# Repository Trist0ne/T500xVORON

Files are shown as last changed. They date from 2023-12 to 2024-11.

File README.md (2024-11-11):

# T500xVORON

A Comgrow T500 Rework to install an RC8 Voron Stealthburner, complete with ChaoticLabs CNC Tap for nozzle based probing and Auto-Z offset, and CANBUS single cable intergration. This should be considered a moderately advanced build; you will need experience or be willing to learn configuring Klipper, crimping/soldering wire, using heat-set inserts, and be comfortable dissasembling/reassembling the T500. If your printer blows up into a million pieces (or otherwise doesn't work like you want it to), you are responsible. I've been running this setup for the better part of a year without issue, and there are several other VoronT500's out there in the wild running nicely. I did my best to document my process and make the configurations foolproof, but I may have missed something somewhere. You may need to use your brain a bit to troubleshoot! Respective rights and thanks go to the VORON team of course, as well as BTT and CHAOTICLABS for their documentation.

The guide below will cover the full T500 conversion; you may be able to deviate if you just want parts of it (for example; enabling sensorless homing on your stock T500) or you want to use different components (such as a different toolhead board, different CANBUS adapter, or not using CANBUS at all), but you're on your own if you do so.

## Why would I want this?
* VORON TAP is far more accurate than the stock inductive Z probe, and is not prone to thermal drift. 
* TAP allows for automatic Z offset, every print, regardless of print surface. "Always perfect first layers"!
* The modular design allows you to change out hotends easily, or use different hotend styles than the stock one. This also makes maintenance or failure recovery WAY easier.
* The LED's on the hotend can show the current printer status, change as the printer heats up to visually show temperature, and illuminate the nozzle while printing. 
* The VORON Stealthburner allows you to use more off-the-shelf, higher quality components that are easy to obtain and replace. It's difficult to get replacements for Comgrow proprietary parts (parts can take weeks to ship).
* An additional ADXL sensor on the X axis simplifies input shaping.
* Simplified wiring with CANBUS cuts the amount of wires running to the toolhead down to just one unified cable.
* It just damn **looks** cooler.

## TABLE OF CONTENTS
### [THINGS TO BUY](https://github.com/Trist0ne/T500xVORON/blob/main/README.md#things-to-buy)
### [THINGS TO PRINT](https://github.com/Trist0ne/T500xVORON/blob/main/README.md#things-to-print)
### [THE BUILD](https://github.com/Trist0ne/T500xVORON/blob/main/README.md#the-build)
#### [> PREREQUISITES](https://github.com/Trist0ne/T500xVORON/blob/main/README.md#prerequisites)
#### [> MOUNTING THE TOOLHEAD](https://github.com/Trist0ne/T500xVORON/blob/main/README.md#mounting-the-toolhead)
#### [> RAISING THE BED](https://github.com/Trist0ne/T500xVORON/blob/main/README.md#raising-the-bed)
#### [> WIRING WIRING WIRING](https://github.com/Trist0ne/T500xVORON/blob/main/README.md#wiring-wiring-wiring)
#### [> SOFTWARE CONFIGURATION](https://github.com/Trist0ne/T500xVORON/blob/main/README.md#software-configuration)
#### [> SLICER CONFIGURATION](https://github.com/Trist0ne/T500xVORON/blob/main/README.md#slicer-configuration)
#### [> TROUBLESHOOTING NOTES](https://github.com/Trist0ne/T500xVORON/blob/main/README.md#troubleshooting-notes)

## Things to Buy
* [ChaoticLabs CNC TAP **V2**](https://chaoticlab.xyz/products/cnc-voron-tap). This is the nozzle probing system. It MUST be the V2
* [BTT U2C V2.1 CANBUS USB adapter](https://www.amazon.com/BIGTREETECH-Adapter-Supports-Connection-Interface/dp/B0B1X47319). This is the USB to CANBUS adapter
* [BTT SB 2209 RP2040](https://biqu.equipment/products/bigtreetech-ebb-sb2209-can-v1-0?variant=40377392431202). This is the toolhead control board. You should get the 2209 **RP2040** variant.
* [Everything from Fasteners & Electronics section of the BOM of the latest VORON Stealthburner](https://vorondesign.com/voron_stealthburner). Do not cheap out on the BMG extruder kit!
* [A Stealthburner compatible Hotend of your choosing](https://us.store.bambulab.com/products/complete-hotend-assembly-x1-series). I use the Bambu Labs hardened steel hotend assembly, but any stealthburner compatible hotend will work.
  * If you use a Bambu Labs hotend, [this](https://www.printables.com/model/322091-voron-stealthburner-printhead-for-bambu-x1cx1-hote) adapter for the StealthBurner works well!
* A few extra parts you will need:
  * 4x M3 5x4mm heat set inserts (same ones that VORONs use)
  * 8x M4x40mmm Socket Heat Cap Screws (Or whatever style M4x40mm screws you would like, SHCS's are just the easiest to tighten during the build)
  * A small length of PTFE tubing for the Stealthburner hotend mount
  * A small spool of 20 AWG wire
  * A small length of double sided mounting tape

## Things to Print
**THESE MUST ALL BE PRINTED FROM ABS OR ASA. THEY ARE DESIGNED FOR ABS. OTHER MATERIALS ARE NOT SUITABLE EITHER DUE TO THEIR TEMPERATURE RESISTANCE OR STRUCTURE CREEP OVER TIME; YOU HAVE BEEN WARNED**
* [1x Complete Voron Stealthburner Assembly](https://github.com/VoronDesign/Voron-Stealthburner/tree/main)
  * Optionally [but highly reccomended!] use the inline filament runout sensor located [here](https://www.printables.com/model/292186-stealthburner-clockwork-2-filament-sensor/files). This replaces the main_body of the CW2 extruder.
  * Ensure you use the Cable_Cover_for_PCB and the toolhead PCB spacer!
  * You do not need to print the gantry mount or TAP mount; the extruder and toolhead cover screw directly into the CNC TAP
* [1x Toolhead Adapter Plate](https://github.com/Trist0ne/T500xVORON/blob/main/STL/Toolhead%20Adapter%20Plate.stl)
* [2x Bed Spacers](https://github.com/Trist0ne/T500xVORON/blob/main/STL/Bed%20Spacer%20T500%20v3.stl). Ensure these print perfectly flat with no warping, or it will throw off your bed level!
* [1x CW2 Cable Bridge](https://github.com/bigtreetech/EBB/blob/master/EBB%20SB2240_2209%20CAN/STL/CW2%20Cable%20Bridge.STL)
* [1x CAN Cable Strain Relief](https://github.com/bigtreetech/EBB/blob/master/EBB%20SB2240_2209%20CAN/STL/Printed_Part_for_CAN_Cable_V1.2.stl)
* [1x U2C Adapter Plate](https://www.printables.com/model/422274-bigtreetech-u2c-mount/files)
  * You will also need some double sided mounting tape to secure this in the electronics bay

Print Settings:
* Layer height: 0.2mm
* Extrusion width: 0.4mm, forced
* Infill percentage: 40%
* Infill type: grid, gyroid, honeycomb, triangle, or cubic
* Wall count: 4
* Solid top/bottom layers: 5
* Supports: NONE

## The Build
You can do the following sections in any order, they are just listed in the order I did them. **Some of the steps will be linked to other guides** for the non-T500 conversion specific parts as they cover them more in depth, and there's no need to reinvent the wheel.

### Prerequisites
* Flash both KATAPULT and Klipper to the U2C CANBUS adapter AND the SB2209 Toolhead board
  * To make your life easier, do this before assembling anything.
  * An excellent resource for CANBUS flashing I reccomend following is located [here](https://github.com/Esoterical/voron_canbus). There are subfolders for the [U2C](https://github.com/Esoterical/voron_canbus/tree/main/can_adapter/BigTreeTech%20U2C%20v2.1) and the [SB2209 rp2040](https://github.com/Esoterical/voron_canbus/tree/main/toolhead_flashing/common_hardware/BigTreeTech%20SB2209%20(RP2040)).
  * You may get stuck here for a bit; this can be a little tricky if you've never done it before, but its not overly difficult. Follow the guide linked above carefully, as the documentation that comes with the boards is a little out of date. Technically you can skip installing KATAPULT and just flash Klipper directly, but it will make updating klipper significantly more difficult later.
  * Technically, flashing Klipper to the U2C is optional. You can probably comment out the "u2c.cfg" and go about your life; it just lets you update and manage it easier, and see it as a temperature sensor in Mainsail. [This](https://docs.meteyou.wtf/btt-u2c-v2.x/klipper-usb-to-can/) guide can help if you get stuck flashing Klipper to the U2C.
  * Pro tip- flashing on the SB2209 rp2040 takes a SECOND. I reran the process many times becuase I thought surely it was failing, but it really does just take a moment to flash. 
* Assemble the VORON Stealthburner
  * Follow the build guide located [here](https://github.com/VoronDesign/Voron-Stealthburner/tree/main/Manual). This is a large step, and your toolhead will only function as well as you assemble it, so take your time.
  * Attach and wire the SB2209 to the Stealthburner, following the build guide [here](https://github.com/bigtreetech/EBB/blob/master/EBB%20SB2209%20CAN%20(RP2040)/Build%20Guide/EBB%20SB2209%20CAN%20V1.0（RP2040）BUILD%20GUIDE_1129.pdf); double check your wiring carefully for the CNC-TAP especially. The colors may not be standard on your TAP wiring, and putting them in the wrong order can fry your TAP sensor.

### Mounting the Toolhead
1. Start by inserting {4x} M3 5x4mm heat set inserts into the adapter plate. Take care to ensure they are perfectly level with the surface of the plastic.

(Ignore the very bottom two holes in the picture; they didn't make it into the final design)

3. Unclip the stock toolhead umbilical and drag chain mount, and move them out of the way. Unmount the stock T500 toolhead and drag chain plate. There are 4 screws around the outside of the plastic casing (keep these!), several screws holding the drag chain plate to the rail. You should be left with a metal rectangular sliding rail.


4. Using the 4 casing screws from the stock toolhead, attach the Adapter Plate to the rectangular sliding rail. Check to ensure the rail still slides back and forth. 


5. Attach the ChaoticLabs CNC TAP to the Adapter Plate
   * The attachment process is the same as the one located in the [CNC TAP build guide](https://github.com/Chaoticlab/CNC-Tap-for-Voron/blob/master/Manual/CNC_Voron_Tap_V2_Build_Guide_20231013.pdf)

6. Attach the Stealthburner assembly to the CNC TAP. Check to make sure the whole assembly can slide up and down (the 'TAP' function)
   * The attachment process for the Stealthburner is the same as the one located in the [CNC TAP build guide](https://github.com/Chaoticlab/CNC-Tap-for-Voron/blob/master/Manual/CNC_Voron_Tap_V2_Build_Guide_20231013.pdf)
   * Ensure you attach the cable bridge shown at the end of the build guide. We will not use the steel wire, but the bridge will provide strain relief and stability to the CANBUS cable port.


7. Check clearences, and appreciate how nice the Stealthburner looks mounted on the T500

### Raising the Bed
The stock T500 gantry and bed are mounted in such a way that the gantry cannot drop low enough to touch the nozzle to the bed. Obviously, this is problematic. Because of the way the gantry is designed, there is no easy way to gracefully drop the toolhead low enough; thus, we have to go the other direction and raise the bed!
* "Wont I lose Z height??"
  * Nope! In it's stock form, the T500 Z rails can raise the nozzle up to 550mm. With these spacers in place, you will still have 520mm of Z clearance (though it will still be software limited to 500mm), so there is no lost Z build height!
* "Wont these spacers melt so close to the bed? Are they strong enough?"
  * Nope! They're far enough from the bed that they are well within the longterm operating temperature limit of ABS. ABS also does not stress creep over time, and should remain durable for the life of the printer
 
1. Remove the print surface, and remove the 8x M4 socket head screws using the access holes
   * 

   * If you have a difficult time getting a tool to fit in those holes, you can unbolt every M4 countersunk screw and remove the headbed entirely.
   * If you remove the bed from the bed frame, remove the screws holding the bed drag chain to the bed frame
   * 

2. Carefully raise the bed frame, and align the bed spacers to the long rectangular rails
   * Be very careful not to damage the heatbed wiring!


   * Depending on how much your ABS print shrunk, you may need to slightly drill out the holes in the printed bed spacers; you'll never get them properly aligned unless the screws can slide through the spacers with only light resistance


3. Using 8x M4x40mm screws, bolt the bed frame to the Y axis rails through the spacers. Ensure everything is very tight and does not have any play; you dont want your bed level changing or your bed flying off its rails!


4. If you removed it in step 1, reattach the drag chain to the bed frame

5. Check to ensure the bed is able to slide **all** the way back and forth across its rails. If you did not use M4x40mm screws to attach the spacers, they may stick out from the rails and hit the Y Stepper drivers.

### Wiring Wiring Wiring
Thankfully for the most part we are SIMPLIFYING the wiring rather than making it more complicated. It should go without saying that your printer should be **fully powered off and unplugged** for the next few steps especially.

#### U2C Wiring and Mounting
1. Remove the electronics bay cover
  * There are 6 screws, 4 in the front and two in the back
  * You will have to slide the heatbed back and forth to reach them all

2. Carefully unplug and remove the following items from the printer. You will need to cut zip ties and undo screws where appropriate:
* The stock toolhead umbilical (you will need to cut open the Z axis wiring loom to remove this fully. Do NOT cut or remove the X axis stepper wires)
  * Remove the umbilical from the X axis drag chain; we will still utilize the drag chain. Unscrew the mounts on the drag chain and move it as close to the Z axis rails as you can, then reattach it 
* The X and Y axis endstops (you will need to cut open the Z axis wiring loom to remove this fully. Do NOT cut or remove the X axis stepper wires)
* 

* Flick the switch highlighted below to "ON" to enable sensorless homing
* 

3. Using at least 20 AWG wire, connect the U2C to the T500 power supply
* There are two open attachment points for power and ground on the stock power supply you can utilize. This is an example; please pay attention to which one is negative and which one is positive
* 

* Connect the wires from the +/- power supply to the green VIN/GND points on the U2C
* 
* Do not get them backwards unless you want to fry your boards!!!

4. Insert the jumper included with the U2C on the pins labled 120R, near the USB-C port

5. Mount the U2C in the electronics bay using the printed mount and double sided tape to secure it
* I chose to mount it here 21556689-9E68-4C35-BBAF-199B8BBE90C0_1_201_a

6. Run a USB-C to USB-A cable from the U2C an open USB port under the T500 screen, following the existing cable routing path from the stock mainboard. Zip tie up the excess; keep it neat!

#### Toolhead CANBUS Cable

1. Crimp the end of the long cable included with the SB2209 with the Molex Microfit 4 pin connector that came with the U2C. Take great care that you align CAN_L, CAN_H, GND, and VIN appropriatly (see pinout above; the black 4 pin connector next to the large white one), or you will pop your toolhead board.
* You do not need to shorten the cable; there is room in the electronics back to tuck the slack away nicely.

2. Using the screws on top of the Z axis, move the toolhead mount as far up the Z axis and as far to the right of the X axis as it will go.
* This will determine how much cable length you need

3. Thread the CANBUS cable from the toolhead port through the X axis drag chain, following the same path the stock umbilical cable did into the electronics bay. Use the same anchor points to attach the cable to the edge of the X axis and the bottom of the Z axis
* LEAVE SOME ROOM FOR SLACK. While you want these cables managed nicely, you dont want them routed so tightly that they're damaging the things they're attached to, or the internal wiring. Dont attach it so tightly that the Z axis rips the cable out at max height!
* Route the cable cleanly through the electronics bay to the U2C. Plug it in, then zip tie up the rest of the slack to one of the stock anchor points.
* Zip tie the CANBUS cable to the X axis stepper wire to keep everything clean and organized
* Finally, Zip tie the CANBUS cable to the edge of the drag chain. The plasic mount on the EBB cable will provide plenty of strain relief 0A58DF86-1371-48C0-9A15-90A06EAC607F_1_201_a

#### Wiring Checks
Dont think, just double check them
1. Power supply POSITIVE is wired to U2C VIN. Power supply GROUND is wired to U2C GND
2. CAN_L, CAN_H, GND, and VIN on the CANBUS cable are aligned to the CAN_L, CAN_H, GND, and VIN pins on the U2C

When you're 100% sure everything is lined up, plug your printer in and flip the power on. Check to make sure the stock mainboard, the U2C and the SB2209 all light up (and that nothing goes pop!). When you're satisfied with your work, reinstall the electronics bay cover and screw it back down. 

### Software Configuration

#### Initial Startup
1. SSH into your printer. The username is **mks**, and the password is **makerbase**. Install KAMP on your printer, located [here](https://github.com/kyleisah/Klipper-Adaptive-Meshing-Purging)
2. Access your printers web-ui. In the machine tab, delete ALL the config files.
3. Download the Klipper Configurations folder from this Github ([here](https://github.com/Trist0ne/T500xVORON/tree/main/Klipper%20Configurations)), and upload them ALL to the printer's config section.
* 
3. Configure the annotated sections of **printer.cfg**, **toolboard.cfg**, and **u2c.cfg**. You will need to fill in the canbus_uuid sections to to tell your printer the CAN addresses of your U2C and SB2209, as well as configuring your sensorless homing (info below)
4. Save and click 'firmware restart'; resolve any errors that Klipper may throw, if any (the error message will tell you what the configuration issue is).

#### Z Endstop Check
**DO THIS BEFORE ATTEMPTING TO HOME THE PRINTER**
1. Once Klipper has successfully loaded and can interface with the U2C and SB2209, navigate to the machine page of the web UI and press 'sync endstops'
2. Endstop Z should be 'OPEN'
3. By hand, move the toolhead up to the top of it's travel to trigger the CNC TAP sensor. Hold it in place and click the 'sync enstops' button. Endstop Z should now be marked as 'CLOSED'
4. Additionally, there should be a blue light on the rear of the TAP sensor that turns red when triggered. If this doesn't happen, you've either wired the sensor wrong or it is faulty.

#### Sensorless Homing Configuration
**DO THIS BEFORE ATTEMPTING TO HOME THE PRINTER**
1. Follow the guide located [here](https://docs.vorondesign.com/community/howto/clee/sensorless_xy_homing.html) to calibrate the sensorless homing.
* The default configurations are made to work with sensorless homing, and are largely preconfigured. You can start from "Finding the right StallGuard threshold". You do not need to add sensorless homing macros, I built them in. Ensure that your sensitivity numbers are high enough that you do not damage the printer, but low enough that the machine is consistently able to home itself.

#### Z Offset Configuration
Update your Z offset
* Remember, with Tap, your nozzle IS the probe. You'll need to manually calibrate the probe's Z offset by using PROBE_CALIBRATE and your chosen leveling method (I use a sheet of paper)

### Final Checks
1. Ensure that your printer can reliably home X, Y, and Z.
2. Test that your Extruder, Hotend, Hotend Fan, Part Cooling Fan, and [optionally] the runout sensor all work as expected.
3. PID Calibrate your Hotend following [this guide](https://www.obico.io/blog/klipper-pid-tuning/)
4. Follow the [Ellis3dp print tuning guide](https://ellis3dp.com/Print-Tuning-Guide/articles/extruder_calibration.html) to dial in your Stealthburner
5. Configure Input Shaping on both X and Y
* You can reference [this guide](https://www.klipper3d.org/Measuring_Resonances.html#bed-slinger-printers) for help
* Your X axis now has a built in accelerometer. You will still need to plug in the included accelerometer and mount it on the Y axis, the same way you would do on the stock T500.
* I use the SHAPER_CALIBRATE macro for automatic calibration. It will measure both X and Y sequentially and apply the best settings automatically. 

6. Retune your Pressure Advance
* Follow [this guide](https://github.com/SoftFever/OrcaSlicer/wiki/Calibration) from the Orca Slicer wiki. You shold set this number in the Orca Slicer filament profile settings, rather than setting it in the Klipper configs. It will be different for every filament and between brands. 
7. Pat yourself on the back for a job well done! Edit your slicer settings as shown below, and then do a test print!

### Slicer Configuration
1. Edit your printer settings "Machine G-code" tab as follows:
* PRINT_START EXTRUDER=[nozzle_temperature_initial_layer] BED=[bed_temperature_initial_layer_single] CHAMBER=[chamber_temperature]
* PRINT_END
* 
2. In the 'Quality' tab, enable Arc Fitting
3. In the 'Others' tab, enable
* Label Objects
* Exclude Objects

### Troubleshooting Notes
There are two errors you may see in your console when starting a print:
1. Unknown command:"SAVE_LAST_FILE"
2. Error evaluating 'gcode_macro PRINT_START:gcode': jinja2.exceptions.UndefinedError: 'dict object' has no attribute 'BED'
These are caused by the non-standard version of klipperscreen that comes built into the T500, and makes calls to incorrectly labeled markers. **Thankfully, they don't actually impede the printing, so you can ignore them!** You can resolve this by installing the standard version of KlipperScreen using [KIAUH](https://github.com/dw-0/kiauh), which comes built into the T500

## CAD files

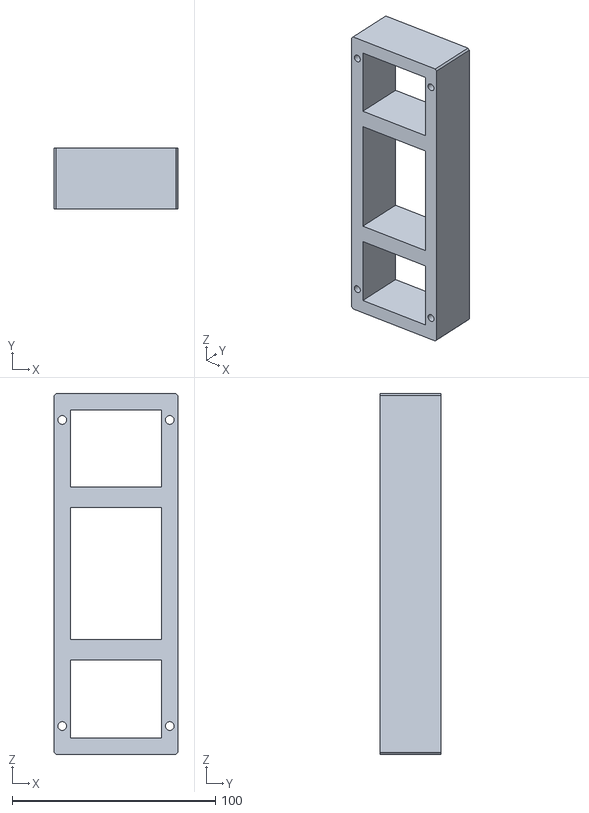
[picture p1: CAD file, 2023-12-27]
STL/Bed Spacer T500 v3.stl
60.9 x 30.0 x 177.5

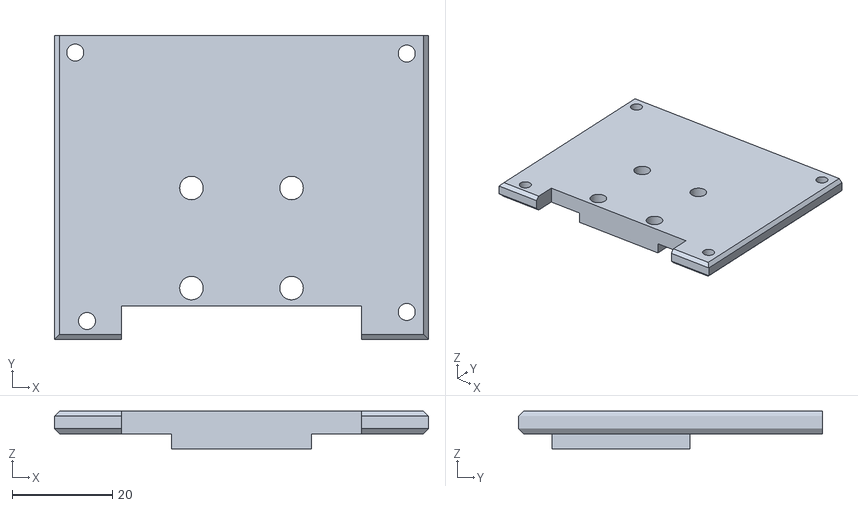
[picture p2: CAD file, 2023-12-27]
STL/Toolhead Adapter Plate.stl
74.8 x 60.7 x 7.50

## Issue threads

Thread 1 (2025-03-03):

Settings for PT1000 Temperature probe

gsargent70, 2025-03-03:
If you are going to use a PT1000 or PT100 temperature probe on your hot end you will need to make the following changes for this guide.

On the SB2209 rp2040 board you will need to wire your probe to the four pin connector rather than the two pin connector.  Please follow the documentation in the SB2209 build guide to see the proper way to crimp your cable.

In the ToolBoard.cfg file you will need to do the following:

In the extruder section comment out sensor_type and sensor_pin lines

Add the following lines to the extruder section

sensor_type: MAX31865
sensor_pin: ToolBoard:gpio9
spi_software_sclk_pin: ToolBoard:gpio10
spi_software_mosi_pin: ToolBoard:gpio8
spi_software_miso_pin: ToolBoard:gpio11
rtd_nominal_r: 100
rtd_reference_r: 430
rtd_num_of_wires: 2

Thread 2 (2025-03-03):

Python 3.8 needed error after updating Klipperscreen

gsargent70, 2025-03-03:
If you decide to update Klipperscreen to eliminate the errors listed in this guide from it being on an old version, you will receive an error about the new version of Klipperscreen needing Python 3.8

Unfortunately there is no good way to update to Python 3.8 with the version of debian on the T500 pad.

To solve this perform these steps after updating Klipperscreen

Log in to the T500 pad via SSH

Enter the following two lines

cd ~/KlipperScreen
git reset --hard v0.4.1

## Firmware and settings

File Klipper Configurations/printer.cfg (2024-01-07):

## CREATED BY @Trist0ne

########################################################################################################################### CONFIG INCLUDES

[include KAMP_Settings.cfg]
[include start.cfg]
[include runout.cfg] ## If you do not use a runout sensor, comment this one out
[include macros.cfg]
[include u2c.cfg]
[include toolboard.cfg]
[include stealthburner_leds.cfg]
[include temperature_led.cfg]

########################################################################################################################### MCU

[mcu]
serial:/dev/serial/by-id/usb-1a86_USB_Serial-if00-port0
restart_method: command

[mcu rpi]
serial: /tmp/klipper_host_mcu

########################################################################################################################### SPEED/ACCEL SETTINGS

[printer]
kinematics: cartesian
max_velocity: 300
max_accel: 3000
max_accel_to_decel: 1500
max_z_velocity: 15
max_z_accel: 100
#square_corner_velocity:2

########################################################################################################################### POWER-ON GCODE

[delayed_gcode set_temeperature_leds]
initial_duration: 1
gcode:
     STATUS_READY

########################################################################################################################### MAINSAIL MISC

[virtual_sdcard]
path: ~/printer_data/gcodes
on_error_gcode: CANCEL_PRINT

[exclude_object]

[pause_resume]

[display_status]

[gcode_arcs]
resolution: 0.1

[idle_timeout]
timeout: 3600 # Idle time (in seconds). This is just the default; it is extended out to 12 hours by the PAUSE macro

########################################################################################################################### INPUT SHAPER

[adxl345 bed]
cs_pin: rpi:None
spi_bus: spidev0.0

[adxl345 hotend]
cs_pin: ToolBoard:gpio1
spi_software_sclk_pin: ToolBoard:gpio2
spi_software_mosi_pin: ToolBoard:gpio0
spi_software_miso_pin: ToolBoard:gpio3

[input_shaper] # Auto configured at the bottom of the config. CONFIGURE YOUR OWN INPUT SHAPER
#shaper_type_x = 3hump_ei
#shaper_freq_x = 52.4
#shaper_type_y = 2hump_ei
#shaper_freq_y = 25

[resonance_tester]
accel_chip_x: adxl345 hotend
accel_chip_y: adxl345 bed
probe_points:250, 250, 20  # an example
accel_per_hz:50
min_freq:1
max_freq:100
max_smoothing:0.2
hz_per_sec:0.5

########################################################################################################################### HEATER CHECKS

[verify_heater extruder]
max_error: 60
check_gain_time:20
hysteresis: 5
heating_gain: 2

[verify_heater heater_bed]
max_error: 240
check_gain_time:180
hysteresis: 5
heating_gain: 1 

########################################################################################################################### STEPPER X

[stepper_x]
step_pin: PE2
dir_pin: PE0
enable_pin: !PE3
microsteps: 16
rotation_distance: 72
endstop_pin: tmc2209_stepper_x:virtual_endstop
#endstop_pin: ^PE15
position_endstop: -6
position_min: -6
position_max: 505
homing_speed: 80
homing_retract_dist: 2
step_pulse_duration:0.000002

[tmc2209 stepper_x]
uart_pin: PE1
diag_pin: ^PE15 # use the same pin that was previously the endstop_pin!
driver_SGTHRS: 255 # 255 is most sensitive value, 0 is least sensitive. Calibrate this yourself
run_current: 1.5
uart_address: 3
#stealthchop_threshold: 999999
driver_TBL: 2
driver_TOFF: 2
driver_HEND: 1
driver_HSTRT: 4
driver_PWM_LIM: 8 
driver_PWM_GRAD: 8
driver_PWM_FREQ: 1
driver_PWM_REG: 4

########################################################################################################################### STEPPER Y

[stepper_y]
step_pin: PB8
dir_pin: !PB6
enable_pin: !PB9
microsteps: 16
rotation_distance: 72
#endstop_pin: ^PE13
endstop_pin: tmc2209_stepper_y:virtual_endstop 
position_endstop: -10
position_min: -10
position_max: 500
homing_speed: 50
homing_retract_dist: 0
step_pulse_duration:0.000002

[tmc2209 stepper_y]
uart_pin: PB7
diag_pin: ^PE13 # use the same pin that was previously the endstop_pin!
driver_SGTHRS: 255 # 255 is most sensitive value, 0 is least sensitive. Calibrate this yourself!
run_current: 1.5
uart_address: 3
#stealthchop_threshold: 999999

[stepper_y1]
step_pin:PD7
dir_pin:PD0
enable_pin:!PB5
microsteps:16
rotation_distance:72
#endstop_pin: ^PE13
endstop_pin: tmc2209_stepper_y:virtual_endstop

[tmc2209 stepper_y1]
uart_pin:PD1
#diag_pin: ^PE13 # use the same pin that was previously the endstop_pin!
#driver_SGTHRS: 255 # 255 is most sensitive value, 0 is least sensitive
run_current:1.5 
uart_address:3
#stealthchop_threshold: 999999

########################################################################################################################### STEPPER Z

[stepper_z]
step_pin: PD15
dir_pin: !PD13
enable_pin: !PA12
microsteps: 16
rotation_distance: 4
endstop_pin:probe:z_virtual_endstop
position_max: 505
position_min: -3
homing_speed: 20

[tmc2209 stepper_z]
uart_pin:PD14
run_current:0.6
uart_address:3
stealthchop_threshold: 999999

[stepper_z1]
step_pin: PD11
dir_pin: !PD9
enable_pin: !PD12
microsteps: 16
rotation_distance: 4
endstop_pin:probe:z_virtual_endstop

[tmc2209 stepper_z1]
uart_pin:PD10
run_current:0.6
uart_address:3
stealthchop_threshold: 999999

########################################################################################################################### BED HEATER

[heater_bed]
heater_pin: PA0
sensor_type: EPCOS 100K B57560G104F
sensor_pin: PC5
#control: pid
#pid_Kp: 75.227
#pid_Ki: 0.807
#pid_Kd: 1748.382
min_temp: 0
max_temp: 95
pwm_cycle_time: 0.0166

########################################################################################################################### Z HOMING

[safe_z_home]
home_xy_position: 250,250
speed: 90
z_hop: 5                 # Move up 5mm
z_hop_speed: 5

########################################################################################################################### PROBE

[probe]
pin: !ToolBoard:gpio22
x_offset: 0
y_offset: 0
z_offset: 0.5 ## CONFIGURE THIS WITH THE Z CALIBRATE TOOL
speed: 10.0
samples: 3
samples_result: median
sample_retract_dist: 3.0
samples_tolerance: 0.006
samples_tolerance_retries: 10
activate_gcode:
    {% set PROBE_TEMP = 180 %}
    {% set MAX_TEMP = PROBE_TEMP + 5 %}
    {% set ACTUAL_TEMP = printer.extruder.temperature %}
    {% set TARGET_TEMP = printer.extruder.target %}

    {% if TARGET_TEMP > PROBE_TEMP %}
        { action_respond_info('Extruder temperature target of %.1fC is too high, lowering to %.1fC' % (TARGET_TEMP, PROBE_TEMP)) }
        M109 S{ PROBE_TEMP }
    {% else %}
        # Temperature target is already low enough, but nozzle may still be too hot.
        {% if ACTUAL_TEMP > MAX_TEMP %}
            { action_respond_info('Extruder temperature %.1fC is still too high, waiting until below %.1fC' % (ACTUAL_TEMP, MAX_TEMP)) }
            TEMPERATURE_WAIT SENSOR=extruder MAXIMUM={ MAX_TEMP }
        {% endif %}
    {% endif %}

########################################################################################################################### BED MESH

[bed_mesh]
speed:190                
horizontal_move_z:3   
mesh_min:26,26   
mesh_max:478,474 
probe_count:10,10    ## you can raise or lower the amount of points probed to speed up meshing or increase mesh accuracy
mesh_pps: 2, 3
algorithm: bicubic
bicubic_tension: 0.2 

########################################################################################################################### Z TILT

[z_tilt]
z_positions: 97, 250
             409, 250
points: 97, 250
        409, 250
speed: 200
horizontal_move_z: 5
retries: 20
retry_tolerance: .001

########################################################################################################################### MAINBOARD FANS

[controller_fan Fan_Board]
pin:PA3
fan_speed: 1.0
idle_timeout: 120
heater: heater_bed, extruder
stepper: stepper_x, stepper_y, stepper_y1, stepper_z, stepper_z1



########################################################################################################################### AUTO GENERATED

#*# <---------------------- SAVE_CONFIG ---------------------->
#*# DO NOT EDIT THIS BLOCK OR BELOW. The contents are auto-generated.
#*#
#*# [extruder]
#*#
#*# [bed_mesh default]
#*# version = 1
#*# points =
#*# 	0.174438, 0.175688, 0.181938
#*# 	0.170688, 0.176938, 0.184438
#*# 	0.193188, 0.194438, 0.198188
#*# x_count = 3
#*# y_count = 3
#*# mesh_x_pps = 4
#*# mesh_y_pps = 4
#*# algo = lagrange
#*# tension = 0.3
#*# min_x = 234.99
#*# max_x = 265.01
#*# min_y = 234.99
#*# max_y = 265.01
#*#
#*# [input_shaper]
#*# shaper_type_x = 2hump_ei
#*# shaper_freq_x = 61.4
#*# shaper_type_y = zv
#*# shaper_freq_y = 30.8
#*#
#*# [heater_bed]
#*# control = pid
#*# pid_kp = 74.862
#*# pid_ki = 0.558
#*# pid_kd = 2509.734

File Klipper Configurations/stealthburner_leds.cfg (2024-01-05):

# Macros for setting the status leds on the Voron StealthBurner toolhead (or for any neopixel-type leds).
#
# You will need to configure a neopixel (or other addressable led, such as dotstar). See
# https://www.klipper3d.org/Config_Reference.html#neopixel for configuration details.


#####################################
#           INSTRUCTIONS            #
#####################################
# How to use all this stuff:
#
#     1.  Copy this .cfg file into your Klipper config directory and then add [include stealthburner_leds.cfg]
#         to the top of your printer.cfg in order to register the LEDs and macros with Klipper.
#     2.  Define your LEDs by editing [neopixel sb_leds] below and entering the data pin from your control board
#         as well as the color order.
#
#           Note: RGB and RGBW are different and must be defined explicitly.  RGB and RGBW are also not able to 
#                 be mix-and-matched in the same chain. A separate data line would be needed for proper functioning.
#
#                 RGBW LEDs will have a visible yellow-ish phosphor section to the chip.  If your LEDs do not have
#                 this yellow portion, you have RGB LEDs.
#
#     3.  Save your config and restart Klipper.
#
#           Note: We set RED and BLUE to 1.0 to make it easier for users and supporters to detect 
#                 misconfigurations or miswiring. The default color format is for Neopixels with a dedicated 
#                 white LED. On startup, all three SB LEDs should light up.
#
#                 If you get random colors across your LEDs, change the color_order to GRB and restart. Then
#                 omit the W for each suggested color_order in the next paragraph.
#
#                 If you get MAGENTA, your  color order is correct. If you get CYAN, you need to use RGBW. If
#                 you get YELLOW, you need to use BRGW (note that BRG is only supported in the latest Klipper
#                 version).
#
#     4.  Once you have confirmed that the LEDs are set up correctly, you must now decide where you want 
#         these macros called up...which means adding them to your existing gcode macros.  NOTHING will happen
#         unless you add the STATUS_????? macros to your existing gcode macros.  
#
#           Example: add STATUS_LEVELING to the beginning of your QGL gcode macro, and then add STATUS_READY 
#                    to the end of it to set the logo LED and nozzle LEDs back to the `ready` state.
#
#           Example: add STATUS_CLEANING to the beginning of your nozzle-cleaning macro, and then STATUS_READY
#                    to the end of it to return the LEDs back to `ready` state.
#
#     5.  Feel free to change colors of each macro, create new ones if you have a need to.  The macros provided below
#         are just an example of what is possible.  If you want to try some more complex animations, you will most
#         likely have to use WLED with Moonraker and a small micro-controller 
#
#####################################
#       END INSTRUCTRUCTIONS        #
#####################################


[neopixel sb_leds]
pin: ToolBoard:gpio16
#   The pin connected to the neopixel. This parameter must be provided.
chain_count: 3
#   The number of Neopixel chips that are "daisy chained" to the
#   provided pin. The default is 1 (which indicates only a single
#   Neopixel is connected to the pin).
color_order: GRBW
#   Set the pixel order required by the LED hardware. Options are GRB,
#   RGB, GRBW, or RGBW. The default is GRB.
initial_RED: 0.0
initial_GREEN: 0.0
initial_BLUE: 0.0
initial_WHITE: 1.0
#   Sets the initial LED color of the Neopixel. Each value should be
#   between 0.0 and 1.0. The WHITE option is only available on RGBW
#   LEDs. The default for each color is 0.#

# Most configuration for the macros can be done by modifying the variables in the _sb_vars macro
# at the start of this file.

##########
# MACROS #
##########

# The following status macros are available (these go inside of your macros):
#
#    STATUS_READY
#    STATUS_OFF
#    STATUS_BUSY
#    STATUS_HEATING
#    STATUS_LEVELING
#    STATUS_HOMING
#    STATUS_CLEANING
#    STATUS_MESHING
#    STATUS_CALIBRATING_Z
#
# With additional macros for basic control:
#
#    SET_NOZZLE_LEDS_ON
#    SET_LOGO_LEDS_OFF
#    SET_NOZZLE_LEDS_OFF
#
# Contributed by Voron discord users wile.e, Tetsunosuke, and etherwalker


[gcode_macro _sb_vars]
# User settings for the StealthBurner status leds. You can change the status colors and led
# configurations for the logo and nozzle here.
variable_colors: {
        'logo': { # Colors for logo states
            'busy': {'r': 0.4, 'g': 0.0, 'b': 0.0, 'w': 0.0},
            'cleaning': {'r': 0.0, 'g': 0.02, 'b': 0.5, 'w': 0.0},
            'calibrating_z': {'r': 0.8, 'g': 0., 'b': 0.35, 'w': 0.0},
            'heating': {'r': 0.3, 'g': 0.18, 'b': 0.0, 'w': 0.0},
            'homing': {'r': 0.0, 'g': 0.6, 'b': 0.2, 'w': 0.0},
            'leveling': {'r': 0.5, 'g': 0.1, 'b': 0.4, 'w': 0.0},
            'meshing': {'r': 0.2, 'g': 1.0, 'b': 0.0, 'w': 0.0},
            'off': {'r': 0.0, 'g': 0.0, 'b': 0.0, 'w': 0.0},
            'printing': {'r': 1.0, 'g': 0.0, 'b': 0.0, 'w': 0.0},
            'standby': {'r': 0.00, 'g': 0.5, 'b': 0.5, 'w': 0.0},
        },
        'nozzle': { # Colors for nozzle states
            'heating': {'r': 0.8, 'g': 0.35, 'b': 0.0, 'w':0.0},
            'off': {'r': 0.0, 'g': 0.0, 'b': 0.0, 'w': 0.0},
            'on': {'r': 0.8, 'g': 0.8, 'b': 0.8, 'w':1.0},
            'standby': {'r': 0.0, 'g': 0.0, 'b': 0.0, 'w':0.0},
        },
        'thermal': {
            'hot': {'r': 1.0, 'g': 0.0, 'b': 0.0, 'w': 0.0},
            'cold': {'r': 0.3, 'g': 0.0, 'b': 0.3, 'w': 0.0}
        }
    }
variable_logo_led_name:         "sb_leds" 
# The name of the addressable LED chain that contains the logo LED(s)
variable_logo_idx:              "1" 
# A comma-separated list of indexes LEDs in the logo
variable_nozzle_led_name:       "sb_leds"
# The name of the addressable LED chain that contains the nozzle LED(s). This will
# typically be the same LED chain as the logo.
variable_nozzle_idx:            "2,3"
# A comma-separated list of indexes of LEDs in the nozzle
gcode:
    # This section is required.  Do Not Delete.


[gcode_macro _set_sb_leds]
gcode:
    {% set red = params.RED|default(0)|float %}
    {% set green = params.GREEN|default(0)|float %}
    {% set blue = params.BLUE|default(0)|float %}
    {% set white = params.WHITE|default(0)|float %}
    {% set led = params.LED|string %}
    {% set idx = (params.IDX|string).split(',') %}
    {% set transmit_last = params.TRANSMIT|default(1) %}

    {% for led_index in idx %}
        {% set transmit=transmit_last if loop.last else 0 %}
        set_led led={led} red={red} green={green} blue={blue} white={white} index={led_index} transmit={transmit}
    {% endfor %}

[gcode_macro _set_sb_leds_by_name]
gcode:
    {% set leds_name = params.LEDS %}
    {% set color_name = params.COLOR %}
    {% set color = printer["gcode_macro _sb_vars"].colors[leds_name][color_name] %}
    {% set led = printer["gcode_macro _sb_vars"][leds_name + "_led_name"] %}
    {% set idx = printer["gcode_macro _sb_vars"][leds_name + "_idx"] %}
    {% set transmit = params.TRANSMIT|default(1) %}

    _set_sb_leds led={led} red={color.r} green={color.g} blue={color.b} white={color.w} idx="{idx}" transmit={transmit}

[gcode_macro _set_logo_leds]
gcode:
    {% set red = params.RED|default(0)|float %}
    {% set green = params.GREEN|default(0)|float %}
    {% set blue = params.BLUE|default(0)|float %}
    {% set white = params.WHITE|default(0)|float %}
    {% set led = printer["gcode_macro _sb_vars"].logo_led_name %}
    {% set idx = printer["gcode_macro _sb_vars"].logo_idx %}
    {% set transmit=params.TRANSMIT|default(1) %}

    _set_sb_leds led={led} red={red} green={green} blue={blue} white={white} idx="{idx}" transmit={transmit}

[gcode_macro _set_nozzle_leds]
gcode:
    {% set red = params.RED|default(0)|float %}
    {% set green = params.GREEN|default(0)|float %}
    {% set blue = params.BLUE|default(0)|float %}
    {% set white = params.WHITE|default(0)|float %}
    {% set led = printer["gcode_macro _sb_vars"].nozzle_led_name %}
    {% set idx = printer["gcode_macro _sb_vars"].nozzle_idx %}
    {% set transmit=params.TRANSMIT|default(1) %}

    _set_sb_leds led={led} red={red} green={green} blue={blue} white={white} idx="{idx}" transmit={transmit}

[gcode_macro set_logo_leds_off]
gcode:
    {% set transmit=params.TRANSMIT|default(1) %}
    _set_logo_leds red=0 blue=0 green=0 white=0 transmit={transmit}

[gcode_macro set_nozzle_leds_on]
gcode:
    {% set transmit=params.TRANSMIT|default(1) %}
    _set_sb_leds_by_name leds="nozzle" color="on" transmit={transmit}

[gcode_macro set_nozzle_leds_off]
gcode:
    {% set transmit=params.TRANSMIT|default(1) %}
    _set_sb_leds_by_name leds="nozzle" color="off" transmit={transmit}
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

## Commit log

2023-12-22 Update folder name
    [filament.cfg, light.cfg, macros.cfg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]
2023-12-22 Saving Work
    [printer.cfg]
2023-12-22 Complete and ready for testing
    [macros.cfg, printer.cfg, sensorless.cfg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]
2023-12-22 Updated and ready to test
    [printer.cfg, start.cfg, toolboard.cfg]
2023-12-27 Add STL's
    [Bed Spacer T500 v3.stl, Toolhead Adapter Plate.stl]
2024-01-05 Update configs
    [Adaptive_Meshing.cfg, KAMP_Settings.cfg, Line_Purge.cfg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]
2024-01-07 Update printer.cfg
    Z tilt tweaks
    [printer.cfg]
2024-01-31 Update README.md
    Added Bambu hotend adapter link
2024-02-21 Update README.md tool board instructions
